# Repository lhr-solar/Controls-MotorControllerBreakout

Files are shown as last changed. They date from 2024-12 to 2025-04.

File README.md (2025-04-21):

TODO: update readme for v2.1: added 2 fan connectors, raised TPS2121 current limit & fuse rating

# Controls-MotorControllerBreakout
Author: Ravi Shah  

This Power and CAN interface board for the Prohelion WaveSculptor 22 Motor Controller allows for easier debugging by switching between controls and external power sources and providing a plug-and-play CANdapter interface.  

## BOM
IBOM: BOM/ibom.html (download and view in browser)  
Mouser Cart: https://www.mouser.com/ProjectManager/ProjectDetail.aspx?AccessID=de9c48e362

## Connectors
| # | Name | Type | Ideal Voltage |
| - | - | - | - |
| J1  | MC CAN 1 | Micro-Fit_3.0_43045-0612_2x03_P3.00mm_Vertical Female | +12V |
| J2  | MC CAN 2 | Micro-Fit_3.0_43650-0215_1x02_P3.00mm_Vertical Female | N/A |
| J3  | CTRLS | Micro-Fit_3.0_43045-0612_2x03_P3.00mm_Vertical Female | +12V |
| J4  | EXT PWR | Micro-Fit_3.0_43650-0215_1x02_P3.00mm_Vertical Female | +12V |
| J5  | CANDAPTER | AMPHENOL_L77SDE09SA4CH3R Female | N/A |

## 3D Model


## PCB


## Schematic
### Root

### Power Distribution

### Power Protection

### LEDs


## Application Note
Controls Leader should always be connected to "CTRLS" with the standard CAN+PWR pinout. The motor controller should always be connected to MC CAN 1 and MC CAN 2. To connect external 12V power, the "EXT EN" jumper must be closed. This jumper can be left closed to allow the power muxing IC to choose a source (prioritizing controls), or it can be left open to ignore the external source. In case of a defective IC, the "MNL" jumper can be closed to permanently connect Controls to the output +12V. Otherwise, the "MNL" jumper should be left open.  

+12v is protected by rectifier diodes and fused on both Controls Leader and this board.  

If using a CANdapter for debugging, the "CAN TERM" jumper must be opened. Otherwise, it should be closed, since this board acts as the terminating end for MotorCAN.

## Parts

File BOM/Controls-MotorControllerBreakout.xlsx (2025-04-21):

Reference | Value | Qty | P/N
C1,C6 | 10u | 2 | C0805C105K3PACTU
C2,C3,C4 | 0.1u | 3 | C0805C104M5RACTU
C5 | 1u | 1 | C0805C105K5PACTU
D1,D3,D4 | -- mixed values -- | 3 | APTD2012LCGCK
D2,D5 | SD12_SOD323 | 2 | SD12C.TCT
D6,D7 | -- mixed values -- | 2 | VSSAF522-M3/H
F1 | 2A | 1 | 0440002.WR
J1,J3 | -- mixed values -- | 2 | 430450612
J2,J4,J6,J7 | -- mixed values -- | 4 | 0436500215
J5 | CANDAPTER | 1 | L77SDE09SA4CH3R
LOGO1,TP1,TP2,TP3,TP4,TP5,TP6 | -- mixed values -- | 7
Q1,Q2 | PMV35EPER | 2 | PMV35EPER
Q3 | RUM001L02T2CL | 1 | RUM001L02T2CL
Q4 | RE1C001ZPTL | 1 | RE1C001ZPTL
R1 | 120 | 1 | CRCW0805120RFKEA
R2,R9,R10,R15 | -- mixed values -- | 4 | CRCW080522K1FKEA
R3,R11 | 100k | 2 | CRCW0805100KFKEAC
R4 | 44.2k (TBD) | 1 | TBD
R5,R8 | 62k | 2 | CRCW080562K0FKEA
R6,R7,R12 | 5k | 3 | CRCW08055K00FKTA
R13 | 51k | 1 | CRCW080551K0FKEA
U1 | TPS2121RUXR | 1 | TPS2121RUXR
Z1,Z2 | BZT52-B12-QX | 2 | BZT52-B12-QX

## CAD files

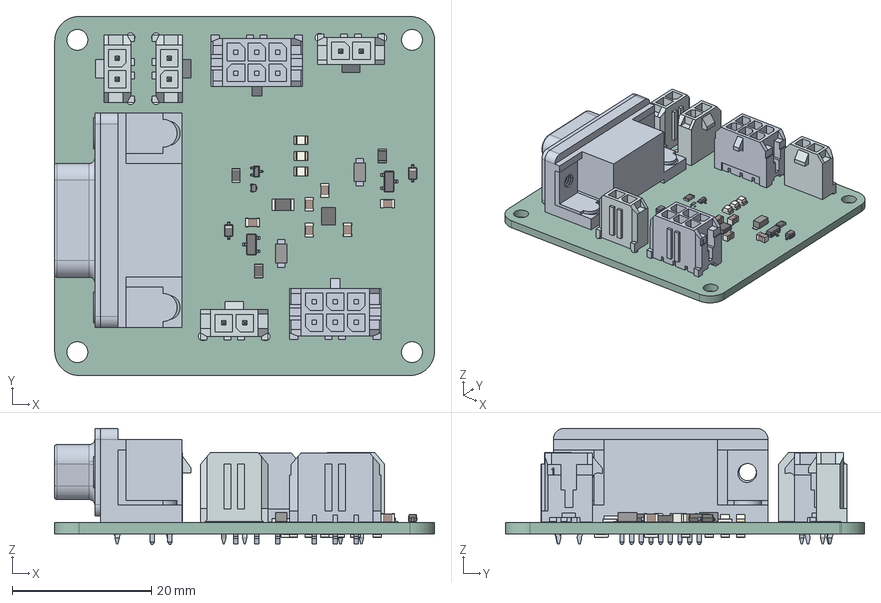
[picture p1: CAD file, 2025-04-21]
3D/Controls-MotorControllerBreakout.step
54.5 x 51.5 x 16.7 mm
ASSEMBLY x 2
436500215wbm000_01 x 4
C_0805_2012Metric x 6
R_0805_2012Metric x 14
Fuse_1206_3216Metric
LED_0805_2012Metric x 3
SOT_23 x 2
D_SOD_323 x 2
RUX0012A_ASM
L77SDE09SA4CH3R
Controls-MotorControllerBreakout_PCB

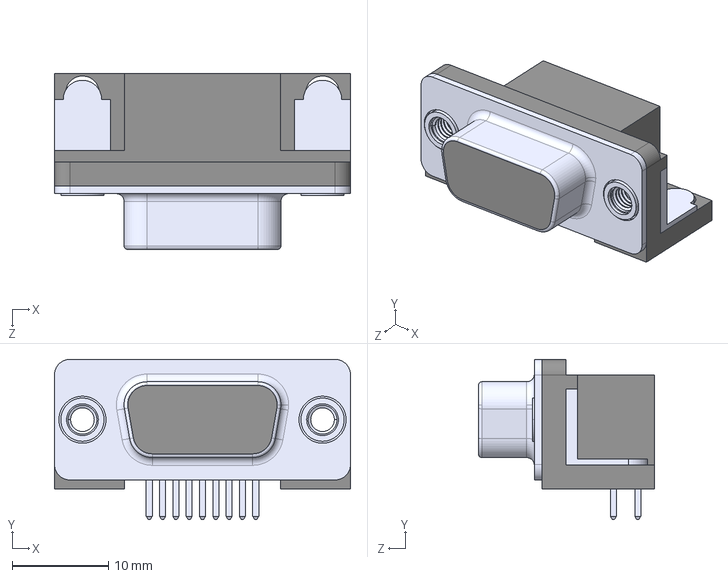
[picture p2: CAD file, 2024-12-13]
Custom-KiCadLibraries/DB-9 Connector/L77SDE09SA4CH3R.step
30.8 x 16.7 x 18.3 mm

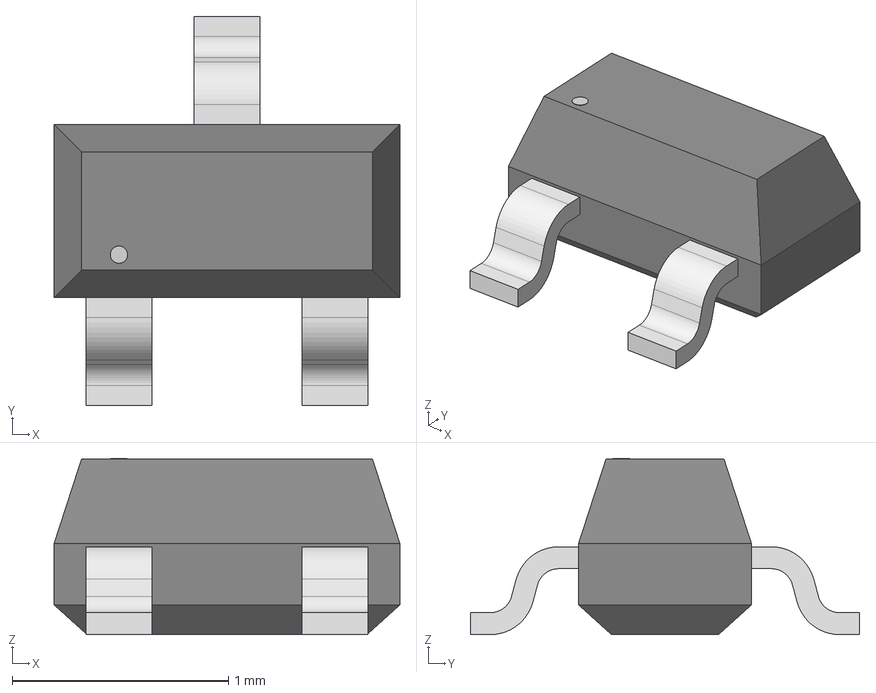
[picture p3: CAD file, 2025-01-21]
Custom-KiCadLibraries/RE1C001ZPTL/TRANS_RE1C001_ROM.step
1.60 x 1.80 x 0.815 mm

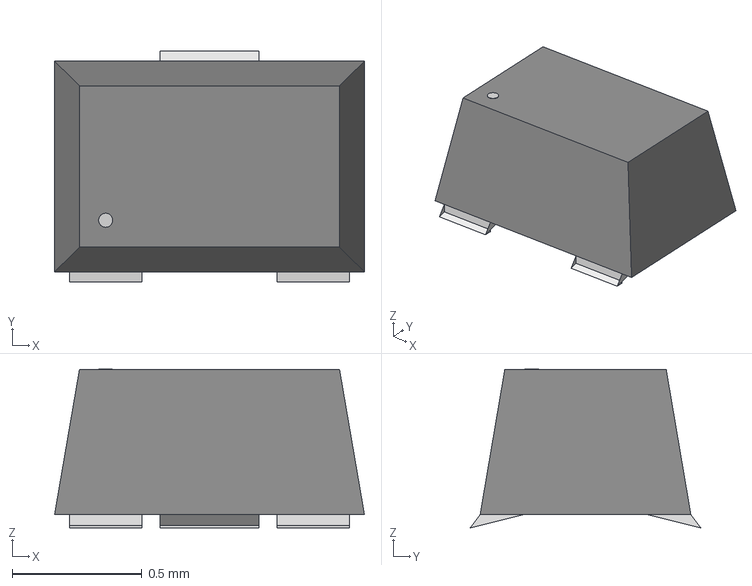
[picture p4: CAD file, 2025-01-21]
Custom-KiCadLibraries/RUM001L02T2CL/TRANS_RUM001_ROM.step
1.19 x 0.889 x 0.612 mm

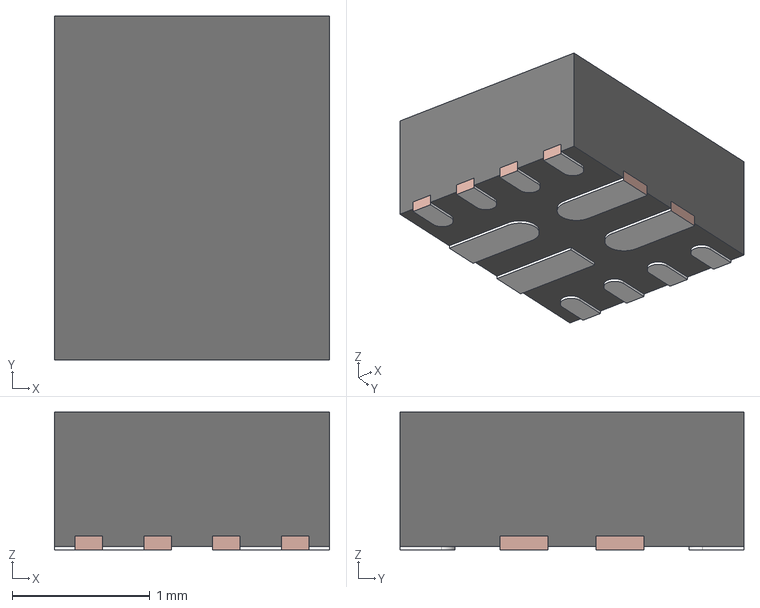
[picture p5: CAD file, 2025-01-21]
Custom-KiCadLibraries/TPS2121/RUX0012A.stp
2.00 x 2.50 x 1.00 mm
FRAME
MOLD

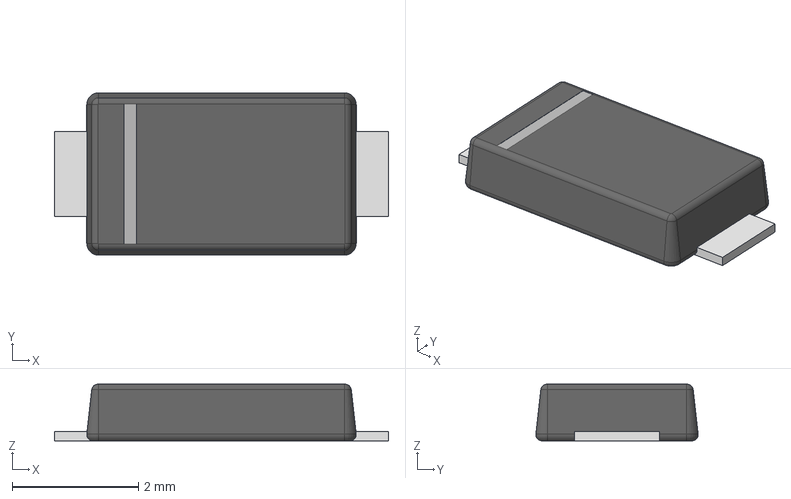
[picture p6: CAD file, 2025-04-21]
Custom-KiCadLibraries/VSSAF522-M3H/DO-221AC (SlimSMA).step
5.30 x 2.58 x 0.9 mm
Pin1
Pin2

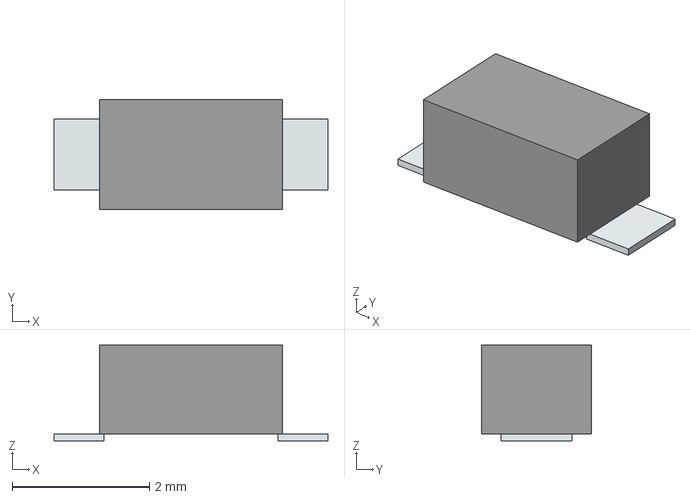
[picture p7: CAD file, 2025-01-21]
Custom-KiCadLibraries/Zener/BZT52-B12-QX.stp
4.00 x 1.60 x 1.40 mm
Pins

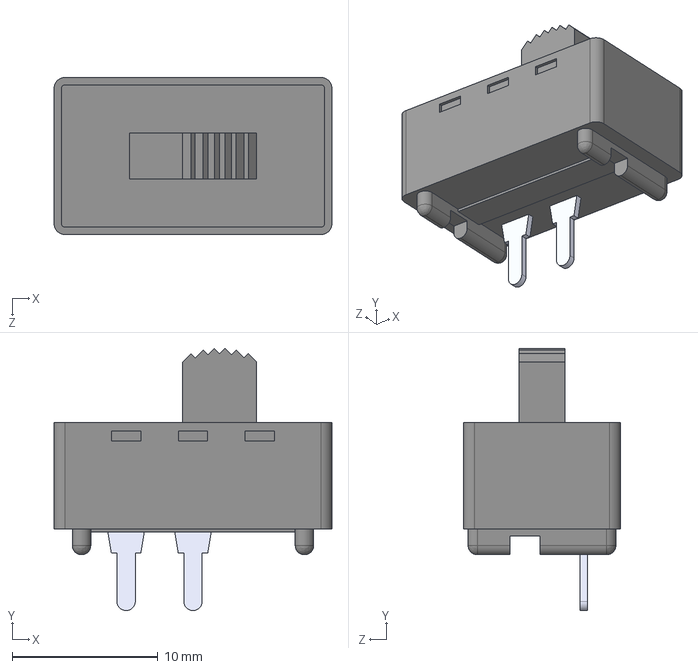
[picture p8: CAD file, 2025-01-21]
Custom-KiCadLibraries/L101011MS02Q/L101011MS02Q.step
19.1 x 18.0 x 10.8 mm

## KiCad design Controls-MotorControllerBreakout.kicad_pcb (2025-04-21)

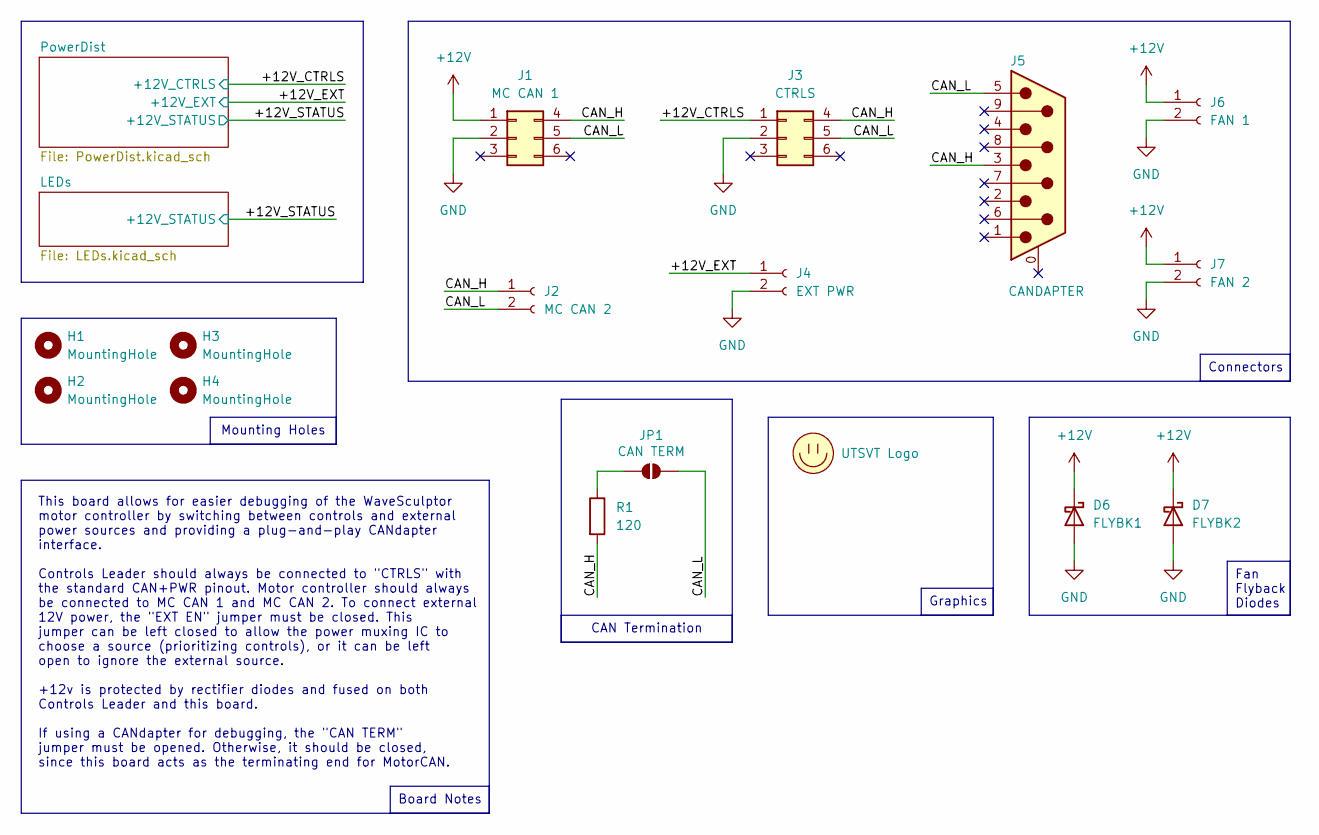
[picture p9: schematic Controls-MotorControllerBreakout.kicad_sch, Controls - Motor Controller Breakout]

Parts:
D6: FLYBK1; DO-221AC
D7: FLYBK2; DO-221AC
H1, H2, H3, H4: MountingHole; MountingHole_3mm
J1: MC CAN 1; Molex_Micro-Fit_3.0_43045-0612_2x03_P3.00mm_Vertical
J2: MC CAN 2; Molex_Micro-Fit_3.0_43650-0215_1x02_P3.00mm_Vertical
J3: CTRLS; Molex_Micro-Fit_3.0_43045-0612_2x03_P3.00mm_Vertical
J4: EXT PWR; Molex_Micro-Fit_3.0_43650-0215_1x02_P3.00mm_Vertical
J5: CANDAPTER; AMPHENOL_L77SDE09SA4CH3R
J6: FAN 1; Molex_Micro-Fit_3.0_43650-0215_1x02_P3.00mm_Vertical
J7: FAN 2; Molex_Micro-Fit_3.0_43650-0215_1x02_P3.00mm_Vertical
JP1: CAN TERM; SolderJumper-2_P1.3mm_Open_RoundedPad1.0x1.5mm
LOGO1: UTSVT Logo; UTSVT_Logo_Symbol
R1: 120; R_0805_2012Metric

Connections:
+12V: D6.1 (K), D7.1 (K), J1.1, J6.1, J7.1; also elsewhere on the board
/+12V_CTRLS: J3.1; also elsewhere on the board
/+12V_EXT: J4.1; also elsewhere on the board
/CAN_H: J1.4, J2.1, J3.4, J5.3, R1.2
/CAN_L: J1.5, J2.2, J3.5, J5.5, JP1.2 (B)
GND: D6.2 (A), D7.2 (A), J1.2, J3.2, J4.2, J6.2, J7.2; also elsewhere on the board
unnamed: JP1.1 (A), R1.1

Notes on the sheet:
Graphics
Board Notes
Fan Flyback Diodes
Mounting Holes
Connectors
CAN Termination
This board allows for easier debugging of the WaveSculptor motor controller by switching between controls and external power sources and providing a plug-and-play CANdapter interface. Controls Leader should always be connected to "CTRLS" with the standard CAN+PWR pinout. Motor controller should alw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

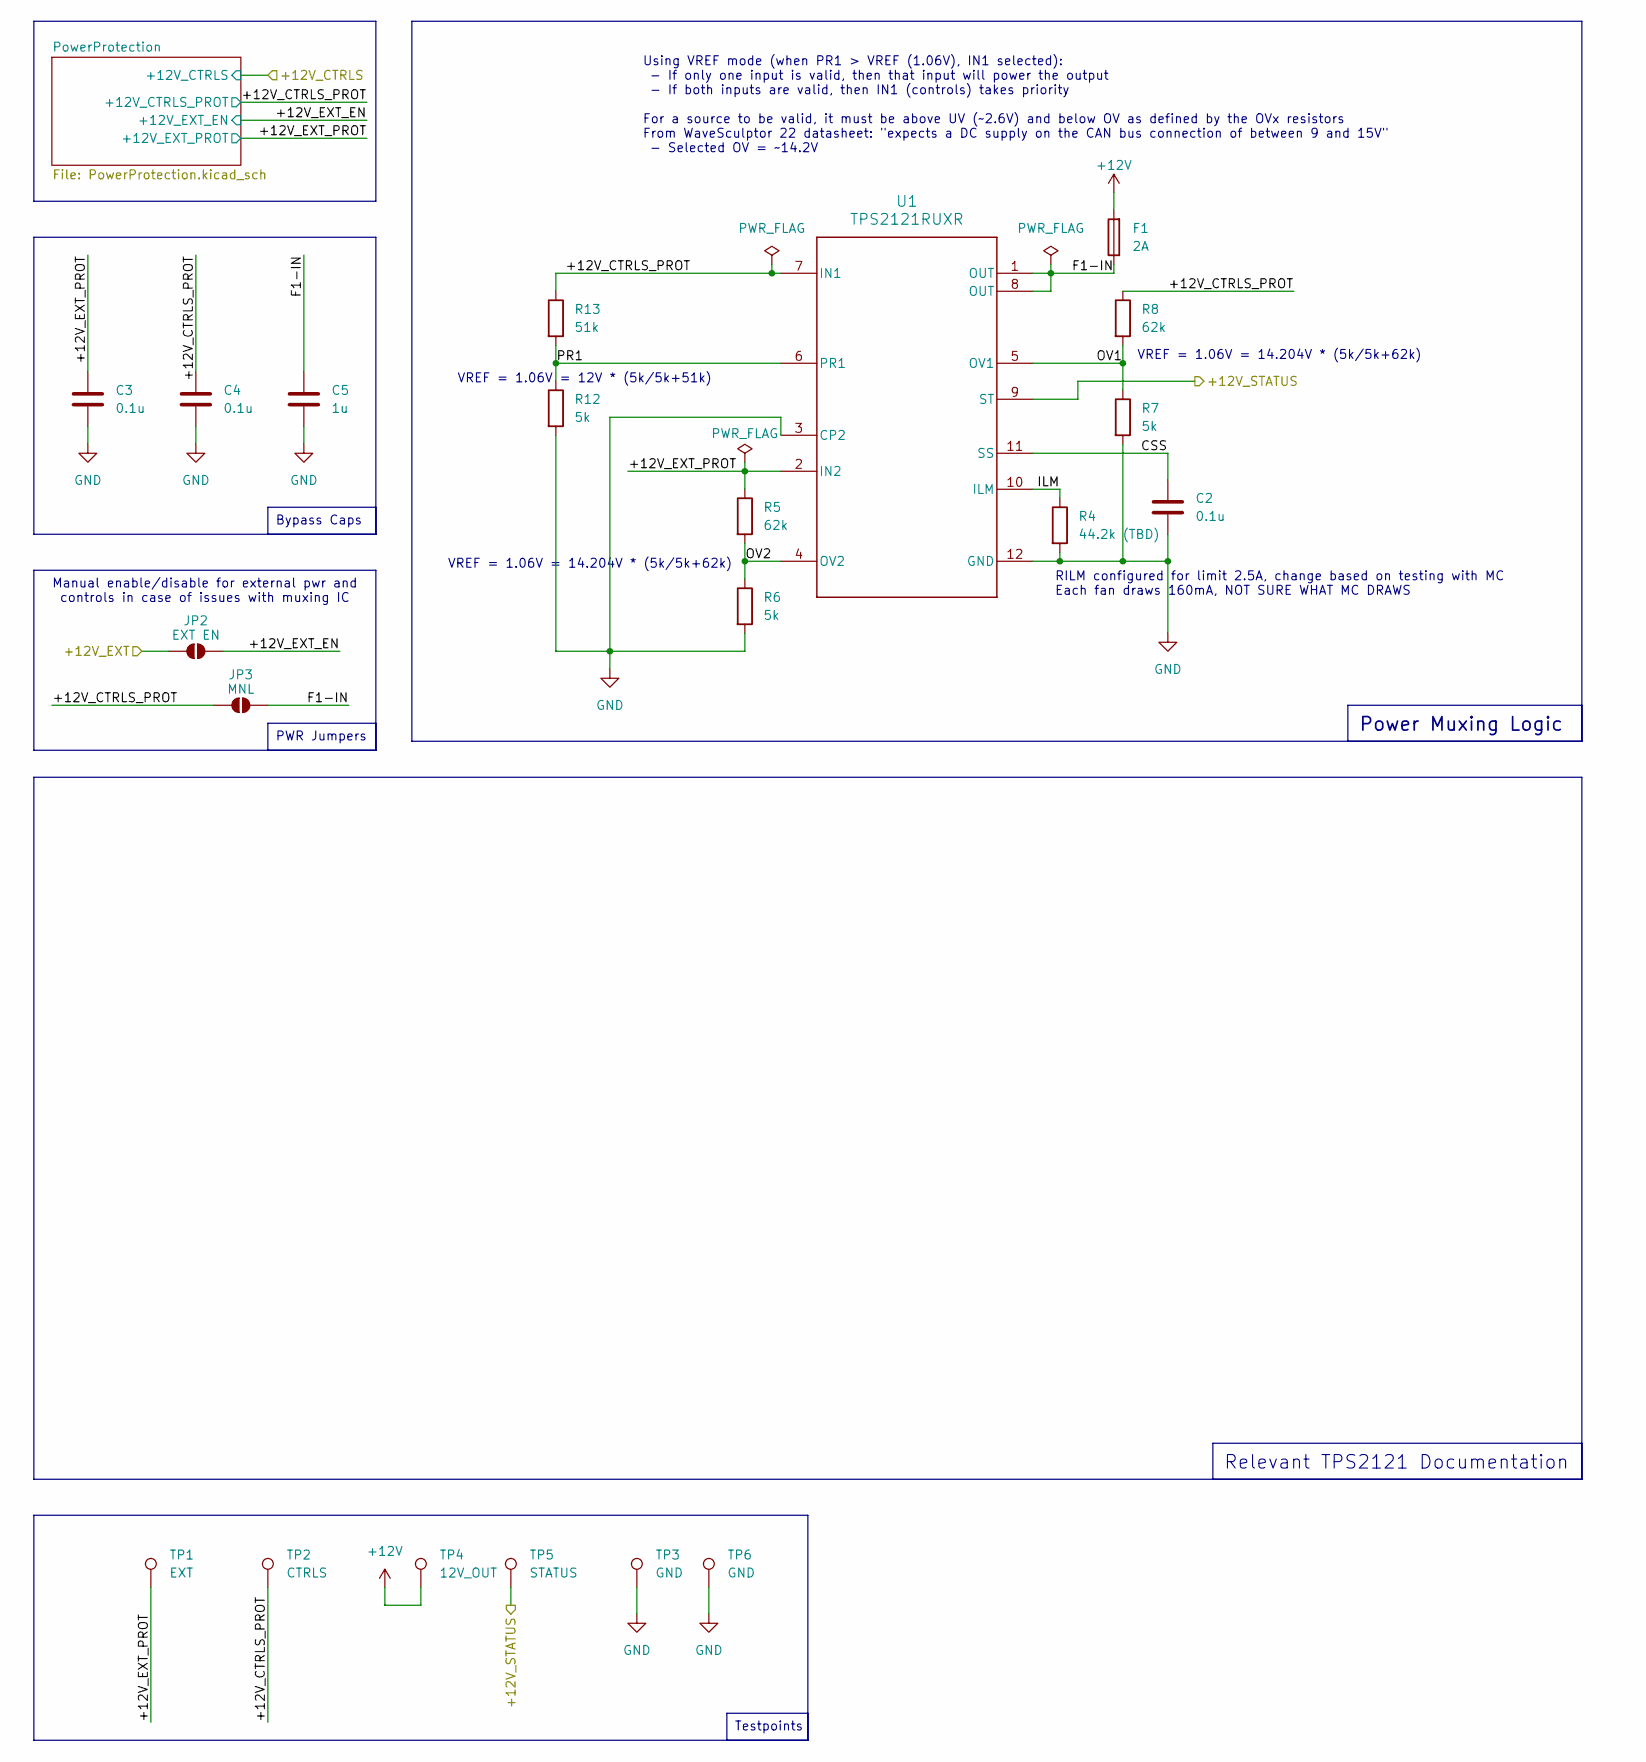
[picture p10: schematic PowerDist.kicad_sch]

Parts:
C2, C3, C4: 0.1u; C_0805_2012Metric
C5: 1u; C_0805_2012Metric
F1: 2A; Fuse_1206_3216Metric; Mouser Part Number 576-0440002.WR
JP2: EXT EN; SolderJumper-2_P1.3mm_Open_RoundedPad1.0x1.5mm
JP3: MNL; SolderJumper-2_P1.3mm_Open_RoundedPad1.0x1.5mm
R4: 44.2k (TBD); R_0805_2012Metric
R5, R8: 62k; R_0805_2012Metric
R6, R7, R12: 5k; R_0805_2012Metric
R13: 51k; R_0805_2012Metric
TP1: EXT; TestPoint_Pad_1.0x1.0mm
TP2: CTRLS; TestPoint_Pad_1.0x1.0mm
TP3, TP6: GND; TestPoint_Pad_1.0x1.0mm
TP4: 12V_OUT; TestPoint_Pad_1.0x1.0mm
TP5: STATUS; TestPoint_Pad_1.0x1.0mm
U1: TPS2121RUXR; RUX0012A

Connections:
+12V: F1.2, TP4.1; also elsewhere on the board
/+12V_EXT: JP2.1 (A); also elsewhere on the board
/+12V_STATUS: TP5.1, U1.9 (ST); also elsewhere on the board
/PowerDist/+12V_CTRLS_PROT: C4.1, JP3.1 (A), R8.1, R13.1, TP2.1, U1.7 (IN1); also elsewhere on the board
/PowerDist/+12V_EXT_EN: JP2.2 (B); also elsewhere on the board
/PowerDist/+12V_EXT_PROT: C3.1, R5.1, TP1.1, U1.2 (IN2); also elsewhere on the board
/PowerDist/CSS: C2.1, U1.11 (SS)
/PowerDist/F1-IN: C5.1, F1.1, JP3.2 (B), U1.1 (OUT), U1.8 (OUT)
/PowerDist/ILM: R4.1, U1.10 (ILM)
/PowerDist/OV1: R7.1, R8.2, U1.5 (OV1)
/PowerDist/OV2: R5.2, R6.1, U1.4 (OV2)
/PowerDist/PR1: R12.1, R13.2, U1.6 (PR1)
GND: C2.2, C3.2, C4.2, C5.2, R4.2, R6.2, R7.2, R12.2, TP3.1, TP6.1, U1.3 (CP2), U1.12 (GND); also elsewhere on the board

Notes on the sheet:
Testpoints
Relevant TPS2121 Documentation
PWR Jumpers
Bypass Caps
Power Muxing Logic
VREF = 1.06V = 14.204V * (5k/5k+62k)
VREF = 1.06V = 12V * (5k/5k+51k)
Using VREF mode (when PR1 > VREF (1.06V), IN1 selected): - If only one input is valid, then that input will power the output - If both inputs are valid, then IN1 (controls) takes priority For a source to be valid, it must be above UV (~2.6V) and below OV as defined by the OVx resistors From WaveScu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
RILM configured for limit 2.5A, change based on testing with MC Each fan draws 160mA, NOT SURE WHAT MC DRAWS
Manual enable/disable for external pwr and controls in case of issues with muxing IC

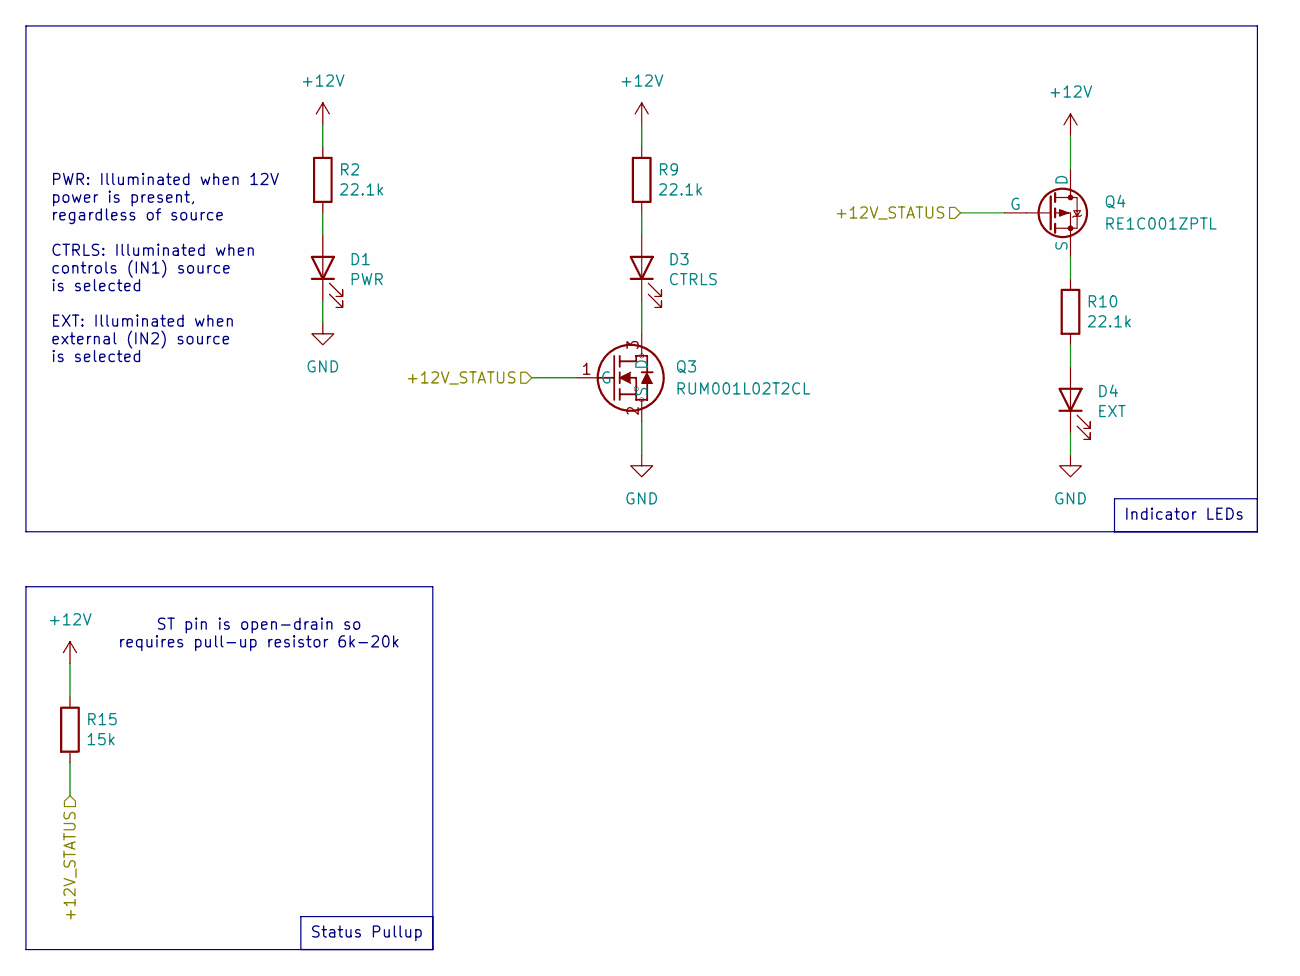
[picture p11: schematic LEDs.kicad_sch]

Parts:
D1: PWR; LED_0805_2012Metric; Mouser Part Number 604-APTD2012LCGCK
D3: CTRLS; LED_0805_2012Metric; Mouser Part Number 604-APTD2012LCGCK
D4: EXT; LED_0805_2012Metric; Mouser Part Number 604-APTD2012LCGCK
Q3: RUM001L02T2CL; TRANS_RUM001_ROM
Q4: RE1C001ZPTL; TRANS_RE1C001_ROM
R2, R9, R10: 22.1k; R_0805_2012Metric; Mouser Part Number 71-CRCW0805-22.1K-E3
R15: 15k; R_0805_2012Metric; Mouser Part Number 71-CRCW0805-22.1K-E3

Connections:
+12V: Q4.1 (D), R2.1, R9.1, R15.1; also elsewhere on the board
/+12V_STATUS: Q3.1 (G), Q4.2 (G), R15.2; also elsewhere on the board
GND: D1.1 (K), D4.1 (K), Q3.2 (S); also elsewhere on the board
unnamed: D1.2 (A), R2.2
unnamed: D3.2 (A), R9.2
unnamed: D3.1 (K), Q3.3 (D)
unnamed: D4.2 (A), R10.2
unnamed: Q4.3 (S), R10.1

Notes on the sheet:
Indicator LEDs
Status Pullup
ST pin is open-drain so requires pull-up resistor 6k-20k
PWR: Illuminated when 12V power is present, regardless of source CTRLS: Illuminated when controls (IN1) source is selected EXT: Illuminated when external (IN2) source is selected

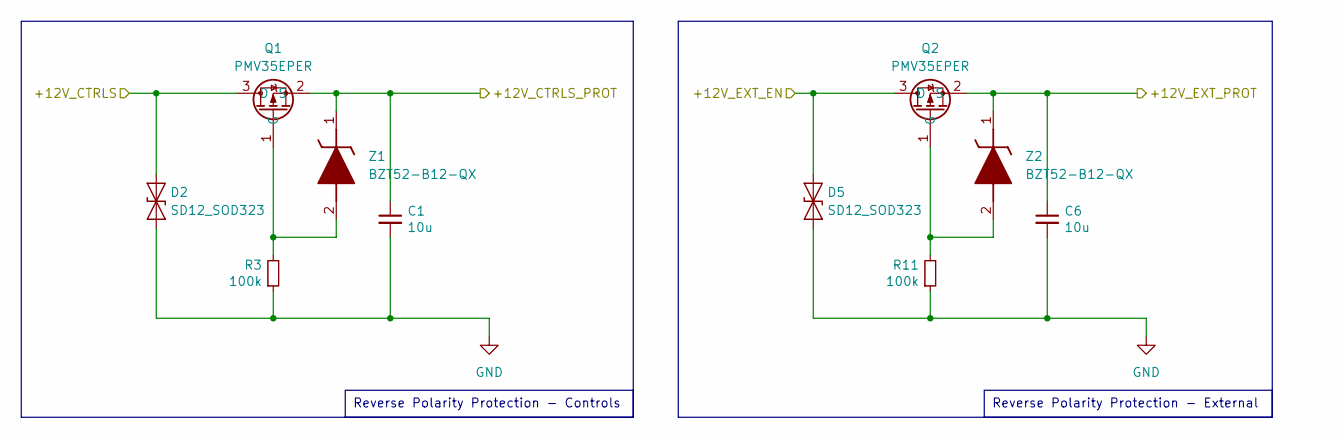
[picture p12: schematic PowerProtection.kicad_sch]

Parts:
C1, C6: 10u; C_0805_2012Metric
D2, D5: SD12_SOD323; D_SOD-323
Q1, Q2: PMV35EPER; SOT-23
R3, R11: 100k; R_0805_2012Metric
Z1, Z2: BZT52-B12-QX; BZT52B12QX; Mouser Part Number 771-BZT52-B12-QX

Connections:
/+12V_CTRLS: D2.2 (A2), Q1.3 (D); also elsewhere on the board
/PowerDist/+12V_CTRLS_PROT: C1.1, Q1.2 (S), Z1.1 (K); also elsewhere on the board
/PowerDist/+12V_EXT_EN: D5.2 (A2), Q2.3 (D); also elsewhere on the board
/PowerDist/+12V_EXT_PROT: C6.1, Q2.2 (S), Z2.1 (K); also elsewhere on the board
GND: C1.2, C6.2, D2.1 (A1), D5.1 (A1), R3.1, R11.1; also elsewhere on the board
unnamed: Q1.1 (G), R3.2, Z1.2 (A)
unnamed: Q2.1 (G), R11.2, Z2.2 (A)

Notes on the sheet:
Reverse Polarity Protection - External
Reverse Polarity Protection - Controls

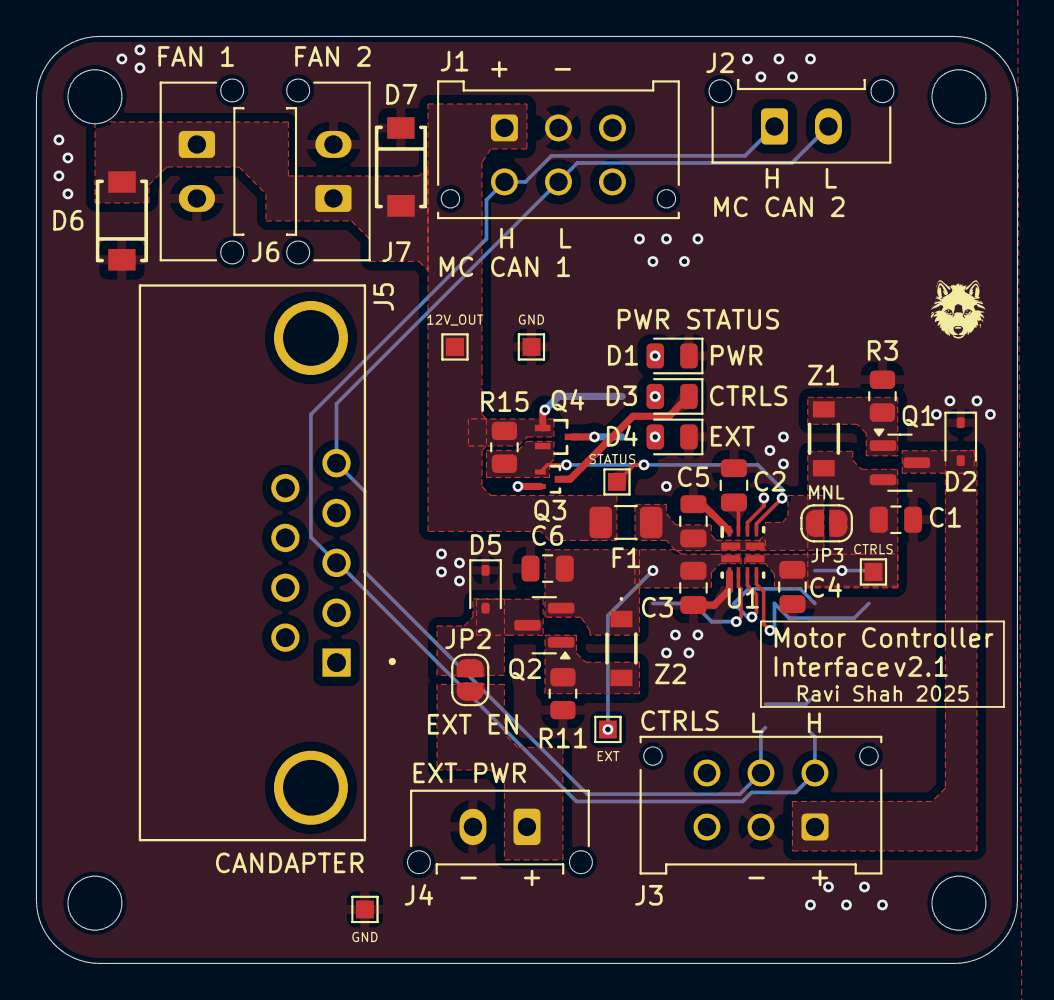
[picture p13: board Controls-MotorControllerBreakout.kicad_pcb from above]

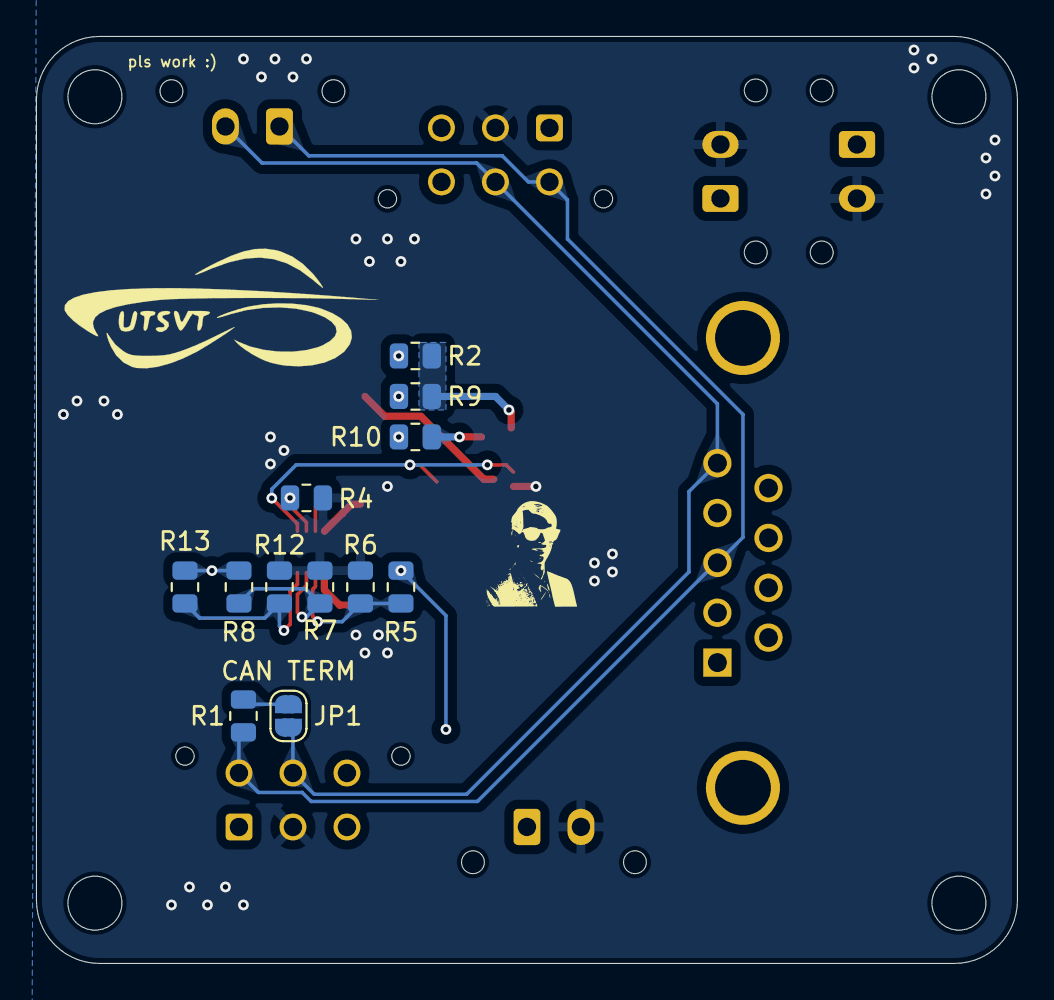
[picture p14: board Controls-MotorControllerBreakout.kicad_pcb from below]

Board: 2 copper layers, 54.5 x 51.5 mm, 56 parts (13 on the bottom side), 24 nets.

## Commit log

2024-11-18 add kicad project
    [Controls-MotorControllerBreakout.kicad_pcb, Controls-MotorControllerBreakout.kicad_sch]
2024-11-18 initial sch
    [Controls-MotorControllerBreakout.kicad_sch]
2024-11-18 add alternative controls conn
    [Controls-MotorControllerBreakout.kicad_pcb, Controls-MotorControllerBreakout.kicad_sch]
2024-11-18 decouple pwr from can
    [Controls-MotorControllerBreakout.kicad_sch]
2024-11-18 pwr led and rm second term resistors
    [Controls-MotorControllerBreakout.kicad_pcb, Controls-MotorControllerBreakout.kicad_sch]
2024-11-19 initial layout/routing
    [Controls-MotorControllerBreakout.kicad_pcb, Controls-MotorControllerBreakout.kicad_sch]
2024-11-19 part numbers
    [Controls-MotorControllerBreakout.kicad_pcb, Controls-MotorControllerBreakout.kicad_sch]
2024-11-19 change diode + models
    [Controls-MotorControllerBreakout.kicad_pcb, Controls-MotorControllerBreakout.kicad_sch, Controls-MotorControllerBreakout.step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]
2024-11-19 fix PP & add dsub conn
    [Controls-MotorControllerBreakout.kicad_pcb, Controls-MotorControllerBreakout.kicad_sch, L77SDE09SA4CH3R.step]
2024-11-19 rm mountingholes
    [Controls-MotorControllerBreakout.kicad_pcb, Controls-MotorControllerBreakout.kicad_sch]
2024-11-19 gerbs + bom
    [Controls-MotorControllerBreakout-B_Cu.gbl, Controls-MotorControllerBreakout-B_Paste.gbp, Controls-MotorControllerBreakout-B_Silkscreen.gbo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]
2024-12-22 separate connector for controls
    [Controls-MotorControllerBreakout.kicad_sch, PowerDist.kicad_sch, PowerProtection.kicad_sch]
2024-12-22 sch is sching (tps2121 design)
    [Controls-MotorControllerBreakout.kicad_sch, PowerDist.kicad_sch, PowerProtection.kicad_sch]
2024-12-23 cleanup sch and add leds
    [Controls-MotorControllerBreakout.kicad_sch, LEDs.kicad_sch, PowerDist.kicad_sch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]
2024-12-26 layout kinda screwy but it works?
    [Controls-MotorControllerBreakout.kicad_pcb, Controls-MotorControllerBreakout.kicad_sch, L101011MS02Q.step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]
2024-12-26 initial layout
    [Controls-MotorControllerBreakout.kicad_pcb, Controls-MotorControllerBreakout.kicad_sch]
2024-12-30 mc interface footprint & better input pours
    [Controls-MotorControllerBreakout.kicad_pcb, Controls-MotorControllerBreakout.kicad_sch]
2025-01-01 better output/CAN routing + testpoints
    [BZT52-B12-QX.stp, Controls-MotorControllerBreakout.kicad_pcb, PowerDist.kicad_sch]
2025-01-10 add reverse polarity for both inputs, fixed muxing logic i think
    [LEDs.kicad_sch, PowerDist.kicad_sch, PowerProtection.kicad_sch]
2025-01-10 proper PR1 pullup
    [PowerDist.kicad_sch]
2025-01-14 symbol/footprint for RUM001L02T2CL
    [LEDs.kicad_sch, TRANS_RUM001_ROM.step]
2025-01-14 LEDs with mosfet
    [LEDs.kicad_sch, TRANS_RE1C001_ROM.step]
2025-01-14 flip connectors so clip faces inside
    [Controls-MotorControllerBreakout.kicad_pcb, LEDs.kicad_sch, PowerDist.kicad_sch]
2025-01-14 fml aghsjkasjksdhksjjfd
    [Controls-MotorControllerBreakout.kicad_pcb]
2025-01-14 start layouting again
    [Controls-MotorControllerBreakout.kicad_pcb, Controls-MotorControllerBreakout.kicad_sch, TRANS_RUM001_ROM.step]
2025-01-15 new tps2121 layout/zones
    [Controls-MotorControllerBreakout.kicad_pcb]
2025-01-16 layout redone
    [Controls-MotorControllerBreakout.kicad_pcb]
2025-01-16 output fuse and solder jumpers
    [Controls-MotorControllerBreakout.kicad_pcb, Controls-MotorControllerBreakout.kicad_sch, PowerDist.kicad_sch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]
2025-01-16 fix silks
    [Controls-MotorControllerBreakout.kicad_pcb]
2025-01-16 STEP + gerbs in root
    [Controls-MotorControllerBreakout.step]
2025-01-22 add detailed board description to readme
2025-01-22 add 3d model, PCB, schematic to readme
2025-01-22 add connectors table to readme
2025-01-22 remove silkscreen comment
    [Controls-MotorControllerBreakout.kicad_pcb]
2025-03-17 add fan conns, layout + routing
    [Controls-MotorControllerBreakout.kicad_pcb, Controls-MotorControllerBreakout.kicad_sch, PowerDist.kicad_sch]
2025-03-19 gerbs, BOM
    [Controls-MotorControllerBreakout.kicad_sch, Controls-MotorControllerBreakout.xlsx]
2025-03-23 flyback sch
    [Controls-MotorControllerBreakout.kicad_sch]
2025-03-24 hi its me again
    [Controls-MotorControllerBreakout.kicad_pcb, Controls-MotorControllerBreakout.kicad_sch, Controls-MotorControllerBreakout.xlsx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]
